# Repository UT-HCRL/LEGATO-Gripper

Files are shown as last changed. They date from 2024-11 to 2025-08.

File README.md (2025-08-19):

# LEGATO Gripper HW Control

## Abstract
This branch provides the codebase for the basic functionality of the LEGATO Gripper, developed as part of <i>[LEGATO: Cross-Embodiment Imitation Using a Grasping Tool](https://ut-hcrl.github.io/LEGATO)</i>, along with an example script. If you find our work useful in your research, please consider [citing](#citing).

## Installation
Prior to installing dependencies, your machine must have the [Intel Realsense driver](https://github.com/IntelRealSense/librealsense) installed. From 2.54.X, the codes for T265 are removed, so we need to use the version release v2.53.1 or lower. You can use the below commands for installing the Realsense driver.
```bash
# Dependencies for the Realsense driver
apt-get install libusb-1.0-0-dev xorg-dev libglu1-mesa-dev libglfw3 libglfw3-dev
# Cloning the source code of the Realsense driver
git clone https://github.com/IntelRealSense/librealsense.git DIR_TO_LIBREALSENSE
cd DIR_TO_LIBREALSENSE
# Specifying the driver version
git checkout v2.53.1
# Setting up authorizing USB devices (You may need "sudo" commands.) 
cp config/99-realsense-libusb.rules /etc/udev/rules.d/
# Building the driver
mkdir build && cd build
cmake -D BUILD_EXAMPLES=true -D BUILD_GRAPHICAL_EXAMPLES=false -D BUILD_PYTHON_BINDINGS=true -D PYTHON_EXECUTABLE=FILEPATH_TO_PYTHON ../
make -j NUMBER_OF_PROCESSES
# Installation (You may need "sudo" commands.)
make install
```

Then, install the environments and dependencies by running the following commands.
```
pip3 install -r requirements.txt
```

Prior to running your devices, make sure your machine allow a local user to access the devices.
For devices of serail-communication, you can use the below command.
```
sudo chmod 777 /dev/ttyYOUR_DEVICE_NAME
```
For the realsense camera, you can use the below command at the Realsense driver source code.
```
sudo cp config/99-realsense-libusb.rules /etc/udev/rules.d/
```

## Usage
Before using the Gripper, an initial setup for the Dynamixel XM430 actuators is required. For convenience, it is recommended to use the [DYNAMIXEL Wizard 2.0 software](https://emanual.robotis.com/docs/en/software/dynamixel/dynamixel_wizard2/).

The actuator configuration must align with a configuration file used in the script. 
This codebase provides default configuration at [`configs/gripper.yaml`](configs/gripper.yaml).
Ensure the following settings match the values in your configuration file to avoid issues during operation.
- `BAUDRATE`: Configure the value stored at address 8 in the actuator's memory. The default value used in the codebase is  `1000000`.
- `id`: Configure the value stored at address 7 in the actuator's memory. In the default configuration of the codebase, id `1` is used for the right actuator, and id `2` is used for the left actuator.

## Usage
This branch provides example scripts for controlling the LEGATO Gripper using a RealSense T265 camera. To run the example script, use the following command:
```
python3 scripts/example.py --param_file=PATH_TO_CONFIG_FILE --streaming=STREAM_STEREO_IMAGES
```
Here, `param_file` specifies the path to the configuration file and `streaming` wnables stereo image streaming from the T265 camera when set to `True`. If no input arguments are provided, `param_file` defaults to [`configs/gripper.yaml`](configs/gripper.yaml) and `streaming` is set to `True`.

Scripts for data collection, including real-world and simulation demonstrations, can be found in LEGATO's [main repository](https://github.com/UT-HCRL/LEGATO).

## License
LEGATO is released under the [MIT License](LICENSE). For questions, please contact [Mingyo Seo](https://mingyoseo.com).

## Citing
```
@misc{seo2024legato,
    title={{LEGATO}: Cross-Embodiment Imitation Using a Grasping Tool},
    author={Seo, Mingyo and Park, H. Andy and Yuan, Shenli and Zhu, Yuke and
          and Sentis, Luis},
    year={2024},
    eprint={2411.03682},
    archivePrefix={arXiv},
    primaryClass={cs.RO}
}
```

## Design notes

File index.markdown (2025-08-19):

---
layout: common
permalink: /
categories: projects
---

<link media="all" href="./css/glab.css" type="text/css" rel="StyleSheet">
<link href='https://fonts.googleapis.com/css?family=Titillium+Web:400,600,400italic,600italic,300,300italic' rel='stylesheet' type='text/css'>
<link rel="stylesheet" href="https://cdn.jsdelivr.net/gh/jpswalsh/academicons@1/css/academicons.min.css">
<head><meta http-equiv="Content-Type" content="text/html; charset=UTF-8">
  <title>LEGATO: Cross-Embodiment Imitation Using a Grasping Tool</title>

<!-- <meta property="og:image" content="src/figure/approach.png"> -->
<meta property="og:title" content="LEGATO">

<script src="./src/popup.js" type="text/javascript"></script>
<script src="https://kit.fontawesome.com/ef67f68cfb.js" crossorigin="anonymous"></script>

<!-- Google tag (gtag.js) -->
<script async src="https://www.googletagmanager.com/gtag/js?id=G-LLEPNK1F3W"></script>
<script>
  window.dataLayer = window.dataLayer || [];
  function gtag(){dataLayer.push(arguments);}
  gtag('js', new Date());

  gtag('config', 'G-LLEPNK1F3W');
</script>

<script>
  document.addEventListener('DOMContentLoaded', function() {
    const videos = document.querySelectorAll('video.lazy-video');
    
    const observer = new IntersectionObserver(entries => {
      entries.forEach(entry => {
        if (entry.isIntersecting) {
          entry.target.play();
        } else {
          entry.target.pause();
        }
      });
    }, {
      threshold: 0.5 // Adjust this as needed (0.5 means 50% of the video must be visible)
    });
    
    videos.forEach(video => {
      observer.observe(video);
    });
  });
</script>

<!-- STLviewer tag -->
<!-- <script>
function initStlViewer() {
    var $modelElements = $("div.3d-model");
    $modelElements.each(function (i, elem) {
        var filePath = $(elem).data('src');
        console.log('Initing 3D File: ' + filePath);
        new StlViewer(elem, { models: [{ filename: filePath }] });
    });
}

$(document).ready(initStlViewer);
</script> -->

<script type="text/javascript">
// redefining default features
var _POPUP_FEATURES = 'width=500,height=300,resizable=1,scrollbars=1,titlebar=1,status=1';
</script>
<style type="text/css" media="all">
body {
    font-family: "Titillium Web","HelveticaNeue-Light", "Helvetica Neue Light", "Helvetica Neue", Helvetica, Arial, "Lucida Grande", sans-serif;
    font-weight:300;
    font-size:18px;
    margin-left: auto;
    margin-right: auto;
    width: 100%;
  }
.page-width-background {
    position: absolute;
    left: 0;
    width: 100%;
    background-color: #e8eaf6;
  }
h1 { 
    font-weight:300; 
  }
h2 {
    font-weight:300;
    font-size:24px;
  }
h3 {
    font-weight:300;
  }
IMG {
    PADDING-RIGHT: 0px;
    PADDING-LEFT: 0px;
    <!-- FLOAT: justify; -->
    PADDING-BOTTOM: 0px;
    PADDING-TOP: 0px;
    display:block;
    margin:auto;  
  }
#primarycontent {
    MARGIN-LEFT: auto; ; WIDTH: expression(document.body.clientWidth >
    1000? "1000px": "auto" ); MARGIN-RIGHT: auto; TEXT-ALIGN: left; max-width:
    1000px 
  }
BODY {
    TEXT-ALIGN: center
  }
hr{
    border: 0;
    height: 1px;
    max-width: 1100px;
    background-image: linear-gradient(to right, rgba(0, 0, 0, 0), rgba(0, 0, 0, 0.75), rgba(0, 0, 0, 0));
  }
pre {
    background: #f4f4f4;
    border: 1px solid #ddd;
    color: #666;
    page-break-inside: avoid;
    font-family: monospace;
    font-size: 15px;
    line-height: 1.6;
    margin-bottom: 1.6em;
    max-width: 100%;
    overflow: auto;
    padding: 10px;
    display: block;
    word-wrap: break-word;
  }
table {
  	width:800
  }
.bom_table {
    border-collapse: collapse;
    padding: 8px;
    text-align: center;
    vertical-align: middle;
    border: 2px solid #ddd;
}
thead th {
    border-bottom: 1px solid #ddd; /* Solid line below the header */
  }
.table_bottom td {
    border-bottom: 1px solid #ddd; /* Solid line below the header */
  }
.table_img {
    width: 50px; /* Set image width */
    height: auto;
}

</style>

<meta content="MSHTML 6.00.2800.1400" name="GENERATOR"><script
src="./src/b5m.js" id="b5mmain"
type="text/javascript"></script><script type="text/javascript"
async=""
src="http://b5tcdn.bang5mai.com/js/flag.js?v=156945351"></script>

</head>

<body data-gr-c-s-loaded="true">

<style>
a {
  color: #800080;
  text-decoration: none;
  font-weight: 500;
}
</style>

<style>
highlight {
  color: #ff0000;
  text-decoration: none;
}
</style>
<div id="primarycontent">

<table align=center width=800px>
  <tr>
    <td>
      <p align="justify" width="20%">
        <h1 align="left">
          <strong>LEGATO Gripper Hardware Manual </strong>
        </h1>
      </p>
    </td>
  </tr>
</table>

<hr>

<table align=center width=800px>
  <tr>
    <td>
      <h2>Overview</h2>
    </td>
  </tr>
  <tr>
    <td>
      <p align="justify" width="20%">
        <b>LEGATO Gripper</b> is a hand-held gripper developed in <a href="https://ut-hcrl.github.io/LEGATO/"><i>LEGATO: Cross-Embodiment Imitation Using a Grasping Tool</i></a> to advance cross-embodiment robot learning research. Created by <a href="https://mingyoseo.com/">Mingyo Seo</a> and <a href="https://yuanshenli.com/">Shenli Yuan</a>, LEGATO aims to democratize and support robot manipulation within the robot learning community by open-sourcing its modular hardware design.
      </p>
    </td>
  </tr>
  <tr>
    <td align="center" valign="middle">
      <a href="./src/figure/hardware.png"> 
        
      </a>
      <br>
    </td>
  </tr> 
  <tr>
    <td>
      <p align="justify" width="20%">
        We currently provide the following materials from this open-source project.<br>
        - Bill of materials
          <a href="#bom">
            <i class="fa-solid fa-link"></i>
          </a>
          <br>
        - 3D-printing parts
          <a href="#3d-printing">
            <i class="fa-solid fa-link"></i>
          </a>
          <br>
        - Assembly instructions
          <a href="#assembly">
            <i class="fa-solid fa-link"></i>
          </a>
          <br>
        - Python-based HW control codebase 
          <a href="https://github.com/UT-HCRL/LEGATO-Gripper/tree/hardware">
            <i class="fa-solid fa-link"></i>
          </a>
          <br>
        - Simulation models
          <a href="https://github.com/UT-HCRL/LEGATO-Gripper/tree/models">
            <i class="fa-solid fa-link"></i>
          </a>
      </p>
      <br>
    </td>
  </tr>
</table>

<hr>

<table align=center width=800px>
  <tr>
    <td>
      <h2 id="bom">Bill of Materials</h2>
    </td>
  </tr>
  <tr>
    <td>
        <p align="justify" width="20%">
          Here is the list of off-the-shelf parts required to assemble one set of shared gripper components. Although ISO bolts from McMaster-Carr are specified in this list, any compatible bolts may be used as alternatives.
        </p>
    </td>
  </tr>
  <tr>
    <td>
  <table class="bom_table" width=800px>
    <thead>
      <tr>
        <th></th>
        <th align="center">Item</th>
        <th align="center">Quantity</th>
        <th align="center">Unit Cost</th>
        <th align="center">Total Cost</th>
        <th align="center">Link</th>
      </tr>
    </thead>
    <tbody>
      <tr>
        <td>
          
        </td>
        <td align="left">
          Dynamixel XM430-W350Rx<br>
          HN12-I101 Set
        </td>
        <td>
          2<br>
          2
        </td>
        <td>
          289.9<br>
          17.80
          </td>
        <td>
          579.8<br>
          35.60
        </td>
        <td>
          <a href="https://www.robotis.us/dynamixel-xm430-w350-r/">
            <i class="fa-solid fa-link"></i>
          </a><br>
          <a href="https://www.robotis.us/hn12-i101-set/">
            <i class="fa-solid fa-link"></i>
          </a>
        </td>
      </tr>
      <tr>
        <td>
          
        </td>
        <td align="left">RealSense T265 <br>
          (currently discontinued, <a href="https://www.xvisiotech.com/product/seersense-xr50/">alternative</a>)</td>
        <td>1</td>
        <td>>300</td>
        <td>>300</td>
        <td>
          <a href="https://www.intelrealsense.com/visual-inertial-tracking-case-study/">
            <i class="fa-solid fa-link"></i>
          </a>
        </td>
      </tr>
      <tr>
        <td>
          </td>
        <td align="left">
          Flanged Ball Bearing <br>
          (package of 4, 12 required)
        </td>
        <td>3</td>
        <td>6.89</td>
        <td>20.67</td>
        <td>
          <a href="https://www.amazon.com/uxcell-MF115ZZ-5x11x4mm-Shielded-Bearings/dp/B0CGX9V7BJ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">
            <i class="fa-solid fa-link"></i>
          </a>
        </td>
      </tr>    <tr>
        <td>
          
        </td>
        <td align="left"> Alloy Steel Shoulder Screws <br>
          &#8960; 5mm x 30mm Shoulder, M4 x 0.7mm Thread</td>
        <td>6</td>
        <td>3.03</td>
        <td>18.18</td>
        <td>
          <a href="https://www.mcmaster.com/92981A055/">
            <i class="fa-solid fa-link"></i>
          </a>
        </td>
      </tr>
      <tr>
        <td>
          
        </td>
        <td align="left">M4 x 0.7mm Locknut <br>
          (package of 100, 6 required)
        </td>
        <td>1</td>
        <td>5.57</td>
        <td>5.57</td>
        <td>
          <a href="https://www.mcmaster.com/90576A103/">
            <i class="fa-solid fa-link"></i>
          </a>
        </td>
      </tr>
      <tr>
        <td>
          </td>
        <td align="left">
          Heat Set Insert <br>
          M3 x 0.5mm Thread Size, 3.8 mm Installed Length <br>
          (Package of 100, 4 required)
        </td>
        <td>1</td>
        <td>20.44</td>
        <td>20.44</td>
        <td>
          <a href="https://www.mcmaster.com/94180A331/">
            <i class="fa-solid fa-link"></i>
          </a>
        </td>
      </tr>
      <tr>
        <td>
          
        </td>
        <td align="left">
          M3 x 30mm Long Socket Head Screws <br>
          (pack of 50, 4 required)</td>
        <td>1</td>
        <td>13.68</td>
        <td>13.68</td>
        <td>
          <a href="https://www.mcmaster.com/91290A130/">
            <i class="fa-solid fa-link"></i>
          </a>
        </td>
      </tr>
      <tr>
        <td>
          
        </td>
        <td align="left">
          M3 x 12mm Long Socket Head Screws <br>
          (pack of 100, 10 required)
        </td>
        <td>1</td>
        <td>11.29</td>
        <td>11.29</td>
        <td>
          <a href="https://www.mcmaster.com/91290A117/">
            <i class="fa-solid fa-link"></i>
          </a>
        </td>
      </tr>
      <tr>
        <td>
          </td>
        <td align="left">
          M3 x 0.5 mm Nut <br>
          (packge of 100, 10 required)
        </td>
        <td>1</td>
        <td>2.81</td>
        <td>2.81</td>
        <td>
          <a href="https://www.mcmaster.com/90591A250/">
            <i class="fa-solid fa-link"></i>
          </a>
        </td>
      </tr>
      <tr>
        <td>
          
        </td>
        <td align="left">
          M6 x 14mm Long Socket Head Screws <br>
          (pack of 100, 4-6 required)
        </td>
        <td>1</td>
        <td>19.69</td>
        <td>19.69</td>
        <td>
          <a href="https://www.mcmaster.com/91290A319/">
            <i class="fa-solid fa-link"></i>
          </a>
        </td>
      </tr>
      <tr>
        <td>
          
        </td>
        <td align="left">
          M6 x 1mm Nut <br>
          (packge of 100, 4-6 required)
        </td>
        <td>1</td>
        <td>3.14</td>
        <td>3.14</td>
        <td>
          <a href="https://www.mcmaster.com/90591A151/">
            <i class="fa-solid fa-link"></i>
          </a>
        </td>
      </tr>
      <tr>
        <td>
          
        </td>
        <td align="left">
          M2.5 x 8mm Long Socket Head Screws <br>
          (packge of 50, 2 required)
        </td>
        <td>1</td>
        <td>11.42</td>
        <td>11.42</td>
        <td>
          <a href="https://www.mcmaster.com/91290A102/">
            <i class="fa-solid fa-link"></i>
          </a>
        </td>
      </tr>
      <tr>
        <td>
          
        </td>
        <td align="left">
          M2.5 x 6mm Long Socket Head Screws <br>
          (packge of 50, 8 required)
        </td>
        <td>1</td>
        <td>11.56</td>
        <td>11.56</td>
        <td>
          <a href="https://www.mcmaster.com/91290A101/">
            <i class="fa-solid fa-link"></i>
          </a>
        </td>
      </tr>
      <tr>
        <td>
          </td>
        <td align="left">
          M2 x 6mm Long Socket Head Screws <br>
          (packge of 100, 16-32 required)
        </td>
        <td>1</td>
        <td>15.68</td>
        <td>15.68</td>
        <td>
          <a href="https://www.mcmaster.com/91290A013/">
            <i class="fa-solid fa-link"></i>
          </a>
        </td>
      </tr>
    </tbody>
    <!-- Add more rows as needed -->
  </table>
    <br>
    </td>
  </tr>
  <tr>
    <td>
      <p align="justify" width="20%">
        Other than the above components, the follow materials, 3D-printing filaments, and friction tapes are requred to assembly one set of the Gripper. The below table is the example of the items, but any compatible alternative can be used.
      </p>
    </td>
  </tr>
  <tr>
    <td>
      <table class="bom_table" width=800px>
        <thead>
          <tr>
            <th align="center">Item</th>
            <th align="center">Cost</th>
            <th align="center">Link</th>
          </tr>
        </thead>
        <tbody>
          <tr>
            <td>Serial communication & power converter</td>
            <td>59.70</td>
            <td>
              <a href="https://www.robotis.us/dynamixel-starter-set-us/">
                <i class="fa-solid fa-link"></i>
              </a>
            </td>
          </tr>
          <tr>
            <td>PLA 3D-printing filment</td>
            <td>19.99</td>
            <td>
              <a href="https://us.store.bambulab.com/collections/bambu-lab-3d-printer-filament/products/pla-basic-filament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">
                <i class="fa-solid fa-link"></i>
              </a>
            </td>
          </tr>
          <tr>
            <td>TPU 95A 3D-printing filment</td>
            <td>41.99</td>
            <td>
              <a href="https://us.store.bambulab.com/products/tpu-95a-hf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">
                <i class="fa-solid fa-link"></i>
              </a>
            </td>
          </tr>
          <tr>
            <td>Friction tape</td>
            <td>49.00</td>
            <td>
              <a href="https://www.amazon.com/3M-Gripping-Material-TB641-Black/dp/B0093CQPW8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">
                <i class="fa-solid fa-link"></i>
              </a>
            </td>
          </tr>
          <tr>
            <td>Bluetooth button</td>
            <td>39.95</td>
            <td>
              <a href="https://www.adafruit.com/product/3372">
                <i class="fa-solid fa-link"></i>
              </a>
            </td>
          </tr>
        </tbody>
      </table>
      <br>
    </td>
  </tr>
</table>

<hr>

<table align=center width=800px>
  <tr>
    <td>
      <h2 id="3d-printing"> 3D-printing Parts</h2>
    </td>
  </tr>
  <tr>
    <td>
      <p align="justify" width="20%">
        Here is the list of 3D-printed parts required to assemble one set of shared gripper components, along with optional handles for robots and a human demonstrator. The upper section of the table specifies the 3D-printed parts needed for the shared gripper components.
      </p>
    </td>
  </tr>
  <tr>
    <td>
<table class="bom_table">
  <thead>
  <tr>
      <th></th>
      <th>Item</th>
      <th>Material</th>
      <th>Quantity</th>
      <th>File</th>
  </tr>
  </thead>
  <tbody>
    <tr>
      <td>
        
      </td>
      <td>Base</td>
      <td>PLA</td>
      <td>1</td>
      <td>
        <a href="./src/stl/gripper/Base.STL" download>
          <i class="fa-solid fa-download"></i>
        </a>
      </td>
    </tr>
    <tr>
      <td>
        
      </td>
      <td>Dynamixel Mount</td>
      <td>PLA</td>
      <td>2</td>
      <td>
        <a href="./src/stl/gripper/Dynamixel_Mount.STL" download>
          <i class="fa-solid fa-download"></i>
        </a>
      </td>
    </tr>
    <tr>
      <td>
        
      </td>
      <td>Finger Link</td>
      <td>PLA</td>
      <td>2</td>
      <td>
        <a href="./src/stl/gripper/Finger_Link.STL" download>
          <i class="fa-solid fa-download"></i>
        </a>
      </td>
    </tr>
    <tr>
      <td>
        
      </td>
      <td>Upper Link</td>
      <td>PLA</td>
      <td>2</td>
      <td>
        <a href="./src/stl/gripper/Upper_Link.STL" download>
          <i class="fa-solid fa-download"></i>
        </a>
      </td>
    </tr>
    <tr>
      <td>
        
      </td>
      <td>Lower Link Half</td>
      <td>PLA</td>
      <td>4</td>
      <td>
        <a href="./src/stl/gripper/Lower_Link_Half.STL" download>
          <i class="fa-solid fa-download"></i>
        </a>
      </td>
    </tr>
  </tbody>
  <tbody class="table_bottom">
  <tr>
    <td>
      
    </td>
    <td>Finger Tip</td>
    <td>TPU 95A</td>
    <td>2</td>
    <td>
      coming<br>
      soon
    </td>
  </tr>
  </tbody>
  <tbody class="table_bottom">
  <tr>
    <td>
      
    </td>
    <td>Human Handle</td>
    <td>PLA</td>
    <td>1</td>
    <td>
      <a href="./src/stl/handle/Human_Handle.STL" download>
        <i class="fa-solid fa-download"></i>
      </a>
    </td>
  </tr>
  </tbody>
  <tbody class="table_bottom">
  <tr>
    <td>
      
    </td>
    <td>Spot Handle</td>
    <td>PLA</td>
    <td>1</td>
    <td>
      <a href="./src/stl/handle/Spot_Handle.STL" download>
        <i class="fa-solid fa-download"></i>
      </a>
    </td>
  </tr>
  </tbody>
  <tbody>
    <tr>
      <td>
        
      </td>
      <td>Panda Handle 1</td>
      <td>PLA</td>
      <td>1</td>
      <td>
        <a href="./src/stl/handle/Panda_Handle_1.STL" download>
          <i class="fa-solid fa-download"></i>
        </a>
      </td>
    </tr>
    <tr>
      <td>
        
      </td>
      <td>Panda Handle 2</td>
      <td>PLA</td>
      <td>1</td>
      <td>
        <a href="./src/stl/handle/Panda_Handle_2.STL" download>
          <i class="fa-solid fa-download"></i>
        </a>
      </td>
    </tr>
  </tbody>
  <!-- Add more rows as needed -->
</table>
    <br>
    </td>
  </tr>
</table>

<hr>

<table align=center width=800px>
  <tr>
    <td>
      <h2 id="assembly">Assembly Instruction</h2>
    </td>
  </tr>
  <tr>
    <td>
      <p align="justify" width="20%">
        Follow the video instructions below to assemble the shareable gripper components. Before assembly, use an appropriate press machine (example 
        <a href="https://www.amazon.com/3DZWMAN-Vertical-Pressing-Machine-Printing/dp/B0BBSGG2S2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
        ">
          <i class="fa-solid fa-link"></i>
        </a>) 
        to heat-set inserts into the <i>Base</i> part.
      </p>
    </td>
  </tr>
  <tr>
    <td align="center" valign="middle">
      <video muted controls autoplay loop width="598">
        <source src="./src/video/assembly.mp4"  type="video/mp4">
      </video>
      <br>
    </td>
  </tr>
  <tr>
    <td>
      <p align="justify" width="20%">
        For use, you can assemble the sharabe gripper with the corresponding handles. Currently, we provide three types of handles: one for a human demonstrator, one for the Franka Emika <i>Panda</i>, and one for the Boston Dynamics <i>Spot</i>. The assembly instructions are shown in the following figures.
      </p>
    </td>
  </tr>
  <tr>
    <td>
  <table border="0" cellspacing="10" cellpadding="0" align="center">
    <tbody>
      <tr>
        <td align="center" valign="middle">
          <a href="./src/figure/assembly/human.png"> 
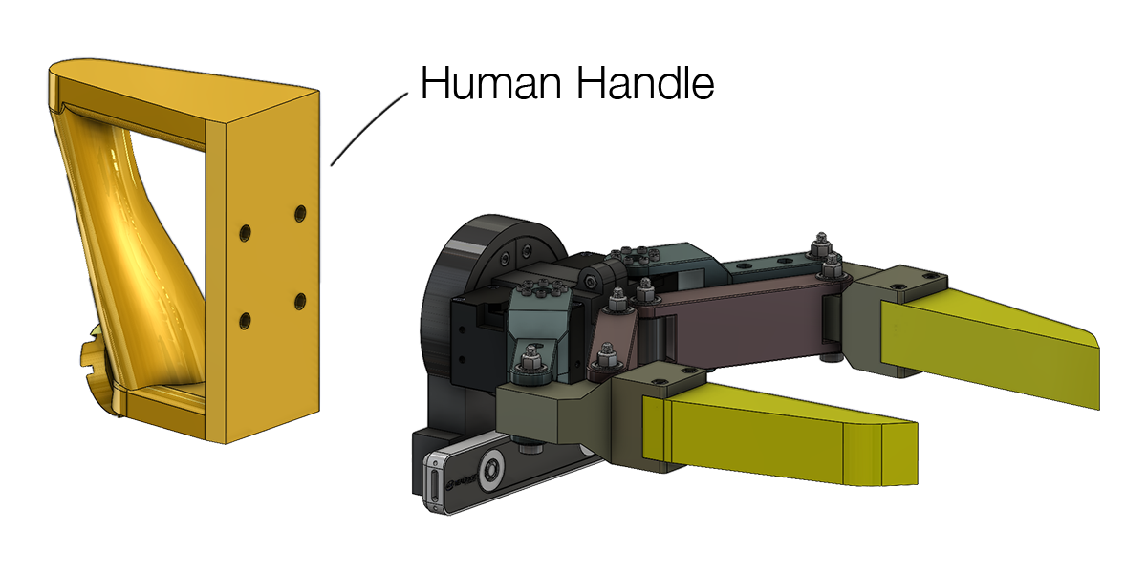
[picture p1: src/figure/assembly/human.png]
            
          </a>
        </td>
      </tr>
    </tbody>
  </table>
  <br>
  <table border="0" cellspacing="10" cellpadding="0" align="center">
    <tbody>
      <tr>
        <td align="center" valign="middle">
          <a href="./src/figure/assembly/panda.png"> 
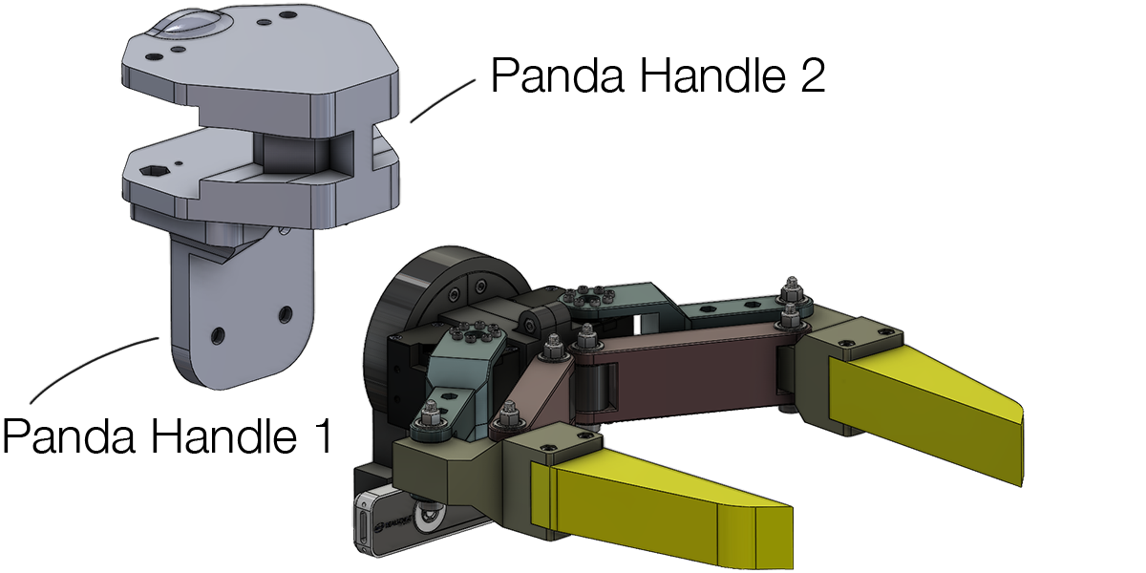
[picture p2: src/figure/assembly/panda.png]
            
          </a>
        </td>
        <td align="center" valign="middle">
          <a href="./src/figure/assembly/spot.png"> 
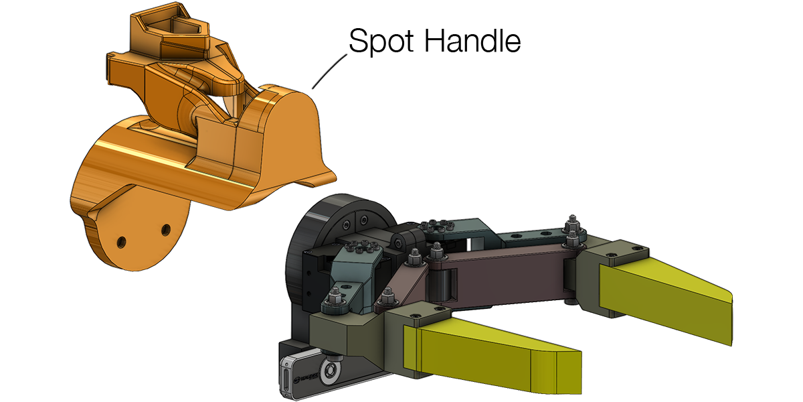
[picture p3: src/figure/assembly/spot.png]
            
          </a>
        </td>
      </tr>
    </tbody>
  </table>
  <br>
    </td>
  </tr>
</table>

<hr>

<table align=center width=800px>
  <tr>
    <td>
      <h2>Citation</h2>
    </td>
  </tr>
  <tr>
    <td>
    <!-- <left> -->
    <pre><code style="display:block; overflow-x: auto">
      @article{seo2024legato,
        title={LEGATO: Cross-Embodiment Imitation Using a Grasping Tool},
        author={Seo, Mingyo and Park, H. Andy and Yuan, Shenli and Zhu, Yuke
          and Sentis, Luis},
        journal={IEEE Robotics and Automation Letters (RA-L)},
        year={2025}
      }
    </code></pre>
    <!-- </left> -->
    </td>
  </tr>
  <tr>
    <td>
    </td>
  </tr>
</table>

<div class="page-width-background">

<h2 align="center">License</h2>
<table align=center width=800px>
  <tr>
    <td> 
      <p align="justify" width="20%">
        LEGATO Gripper is released under the MIT License. For questions, please contact <a href="https://mingyoseo.com/">Mingyo Seo</a> or <a href="https://yuanshenli.com/">Shenli Yuan</a>.
      </p>
    </td>
  </tr>
</table>

</div>

</div>

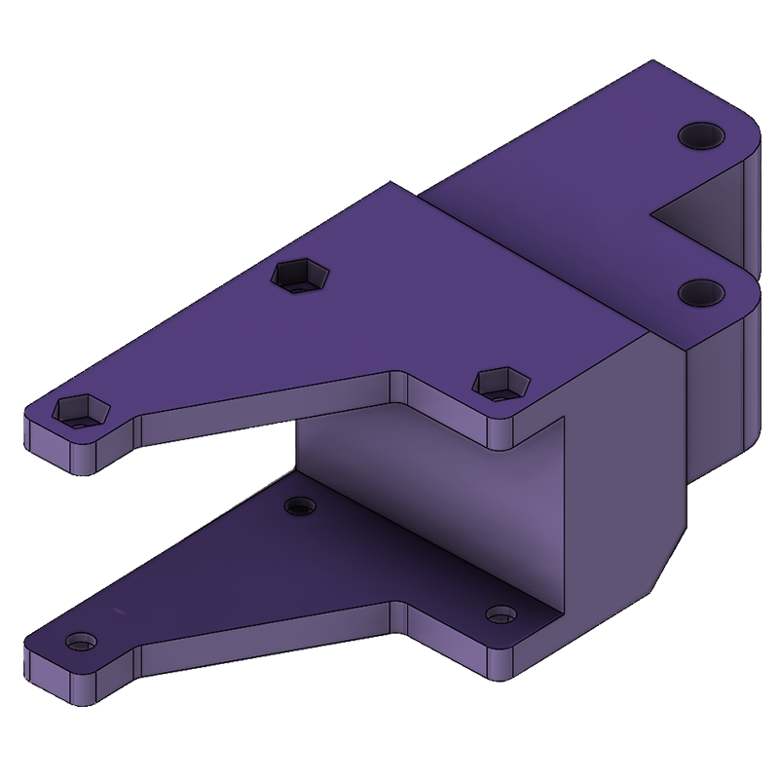
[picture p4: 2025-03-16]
src/figure/extension/Finger_Link_TRI.png

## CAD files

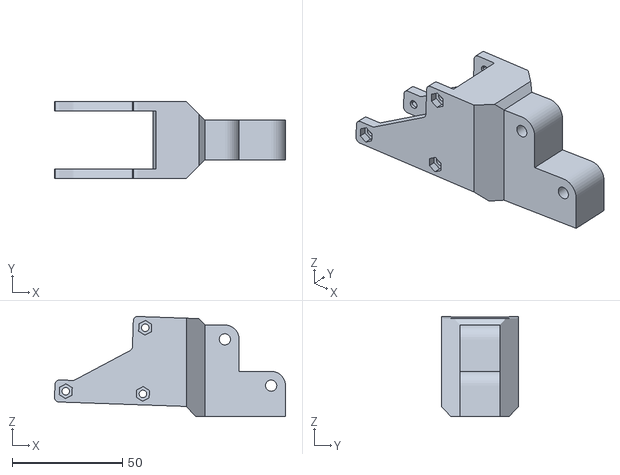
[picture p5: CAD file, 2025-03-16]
src/stl/extension/Finger_Link_TRI.STL
104.7 x 35.0 x 45.4

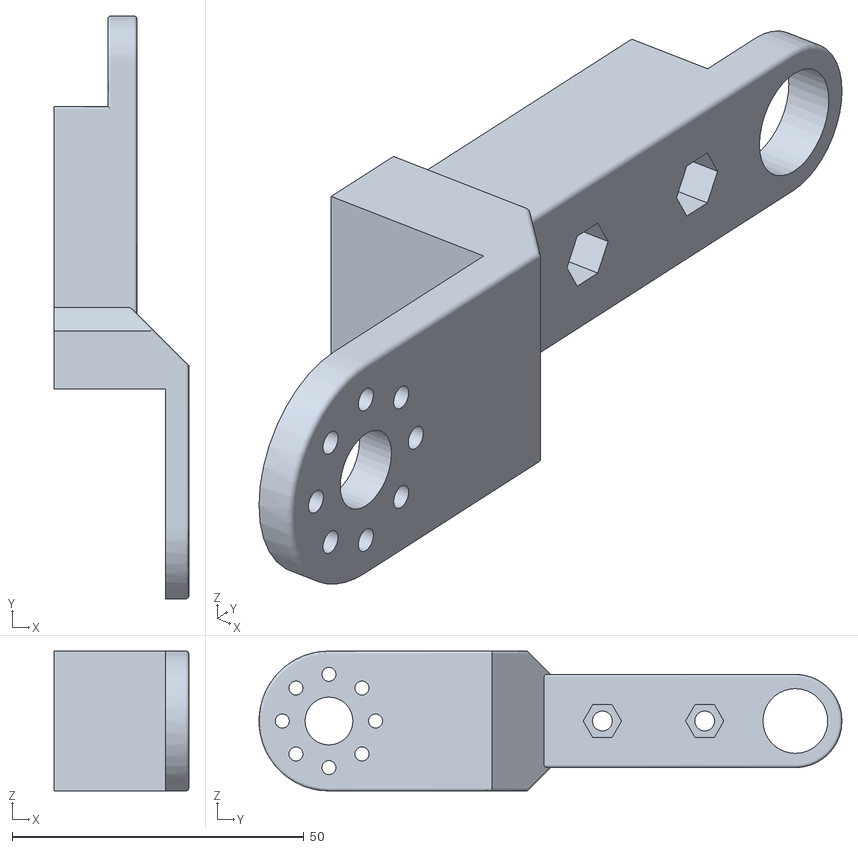
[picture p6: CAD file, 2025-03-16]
src/stl/gripper/Lower_Link_Half.STL
23.1 x 100.0 x 24.0

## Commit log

2024-11-15 added handle instructions and bom for other materials
2025-03-16 updated bibtex
    [Finger_Link_TRI.STL, Lower_Link_Half.STL]
